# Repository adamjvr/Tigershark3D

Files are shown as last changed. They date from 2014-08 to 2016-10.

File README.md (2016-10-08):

Tigershark3D
============

NOTE: Project has been forked into the Archim project by Ultimachine, its the commercial implementation of the Tigershark 3D printer controller prototype. Learn more here: https://github.com/ultimachine/Archim

A TinyG Powered 3D printer controller for RepRap, based on the RAMBo by Ultimachine, the Arduino DUE, and the TinyG from Synthetos.com

More On TinyG Firmware Here:

AVR Version of TinyG

https://github.com/synthetos/TinyG

ARM Version of TinyG

https://github.com/synthetos/g2

- Powered by the TinyG CNC Firmware from Sythetos.com
- Atmel ATSAM3X8E ARM Cortex M3 (DUE)
- Arduino DUE Compatible
- 5 Texas Instruments DRV8825 Stepper Drivers handle up to 2.5A per phase
- 6 MOSFETs for Heat and fans
- Ti TPIC46L01 Low-Side Automotive MOSFET Driver
- 2 MAX31855EASA+ Thermocouple ADCs
- Two Thermistors
- 2A 3.3V Power for Logic
- 3A 5V power for offboard systems and powering 3.3v Logic regulator
- USB bust power jumperable for firmware flashing purposes
- Firmware flashing via BOSSA
- Max/Min Endstops for 3 Axis
- 6 MOSFETs driven with a gate driver off PWM for heat and fans
- Offboard Expansion Port, generic GPIO expansion, and Kinen interface compatible (https://github.com/kinen/kinen/wiki)
-  True Galvanic Isolation of the USB port and full USB 2.0 Speeds

TinyG 2 ARM Firmware Repository: https://github.com/synthetos/g2

BOSSA Atmel SAM Firmware Flashing Tool: https://github.com/shumatech/BOSSA

Rev2 Update:

Tigershark Rev2 saw a large amount of pin function remapping, mostly to correct the PWM issues int he rev1 board. In addition to the corrections in the circuitry Tigershark has been shrunk and reshaped into the same formfactor and breakout as the RAMBo the board that has heavily inspired Tigershark.

Rev2 2D :
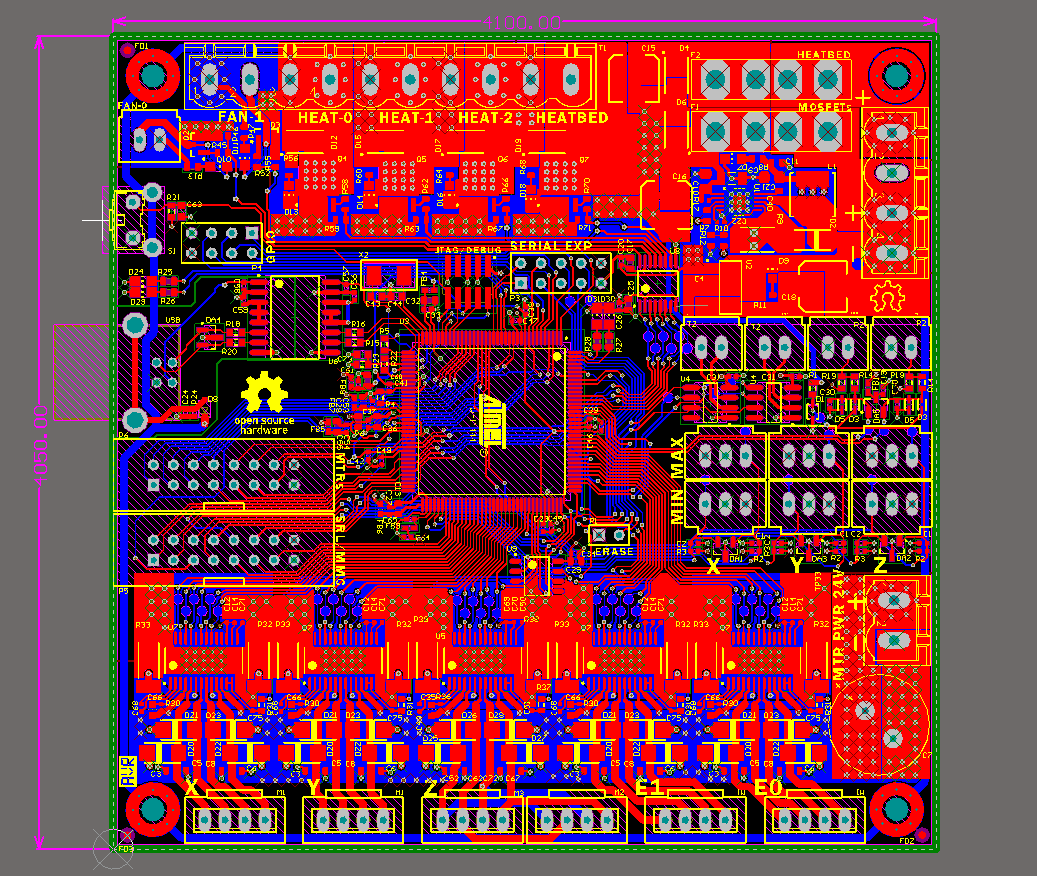
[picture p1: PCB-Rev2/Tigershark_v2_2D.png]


Rev2 3D :
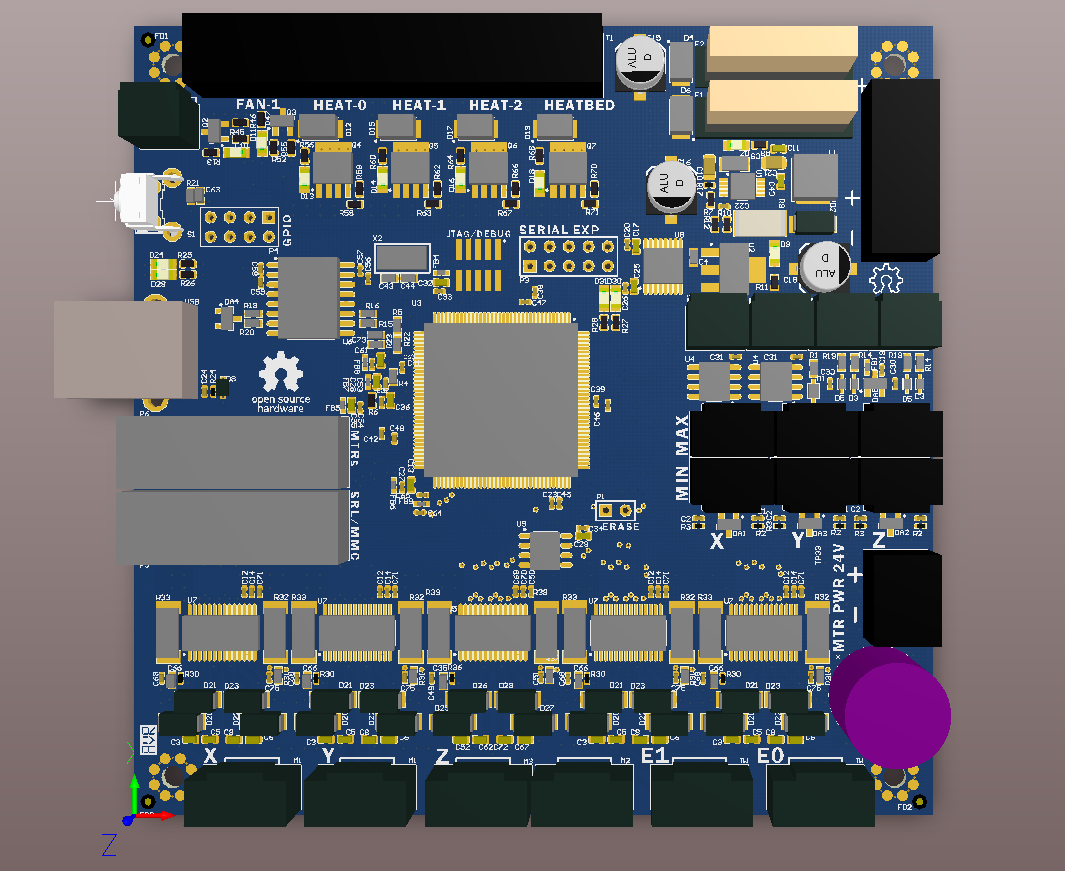
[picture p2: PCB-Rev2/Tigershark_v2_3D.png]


Fabrication Update:

Tigershark rev 1 runs TinyG G2 successfully and connects to Chilipeppr. Rev1 was not without its electrical bugs though, motor ref PWMs for the extruder channels were bound and inverted same issue with two of the mosfets. The rev2 design will have to be repinned to correct these issues. Rev 1 is also too large and expensive and rev2 will see quite a size shrink down and most definitely the same formfactor as the RAMBo. All in all prototype run was successful, all the subsystem circuits have been confirmed and rev2 will be completed soon after. Even though rev2 has to be done to correct the PWM signal issues the plan is to still get rev1 printing so some traces will be cut and jumper wires applied to get it setup to drive a single nozzle reprap.

Rev 1 Fabricated Working Prototype:
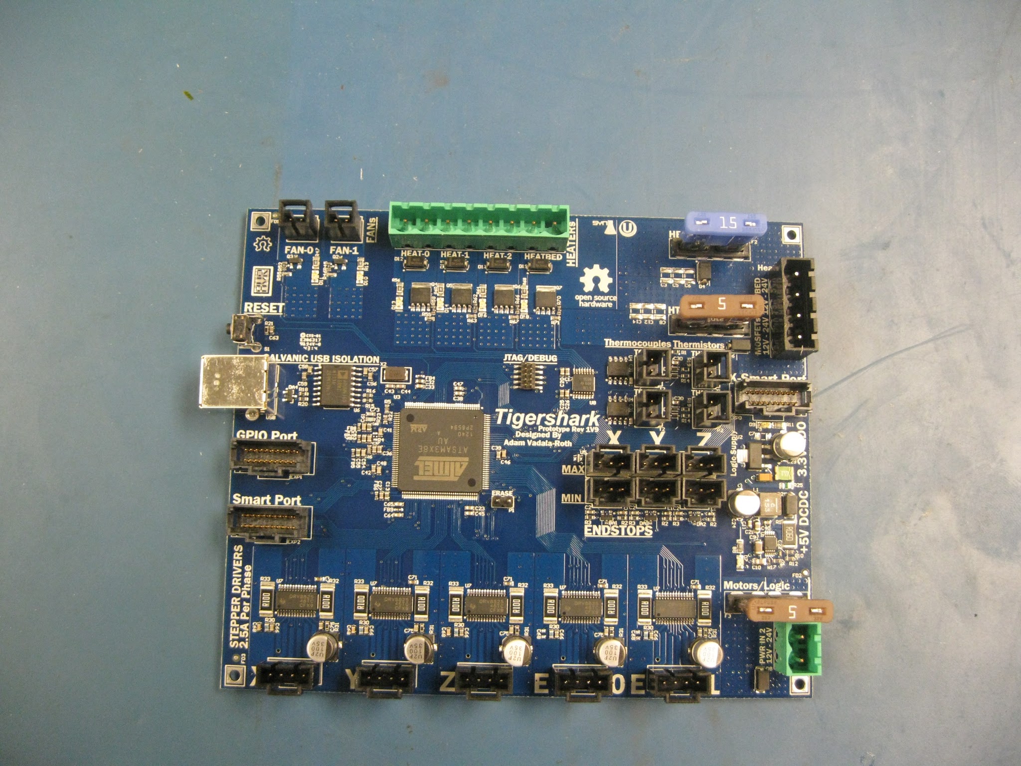
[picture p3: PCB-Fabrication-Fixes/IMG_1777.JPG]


Rev 1 Prototype Design
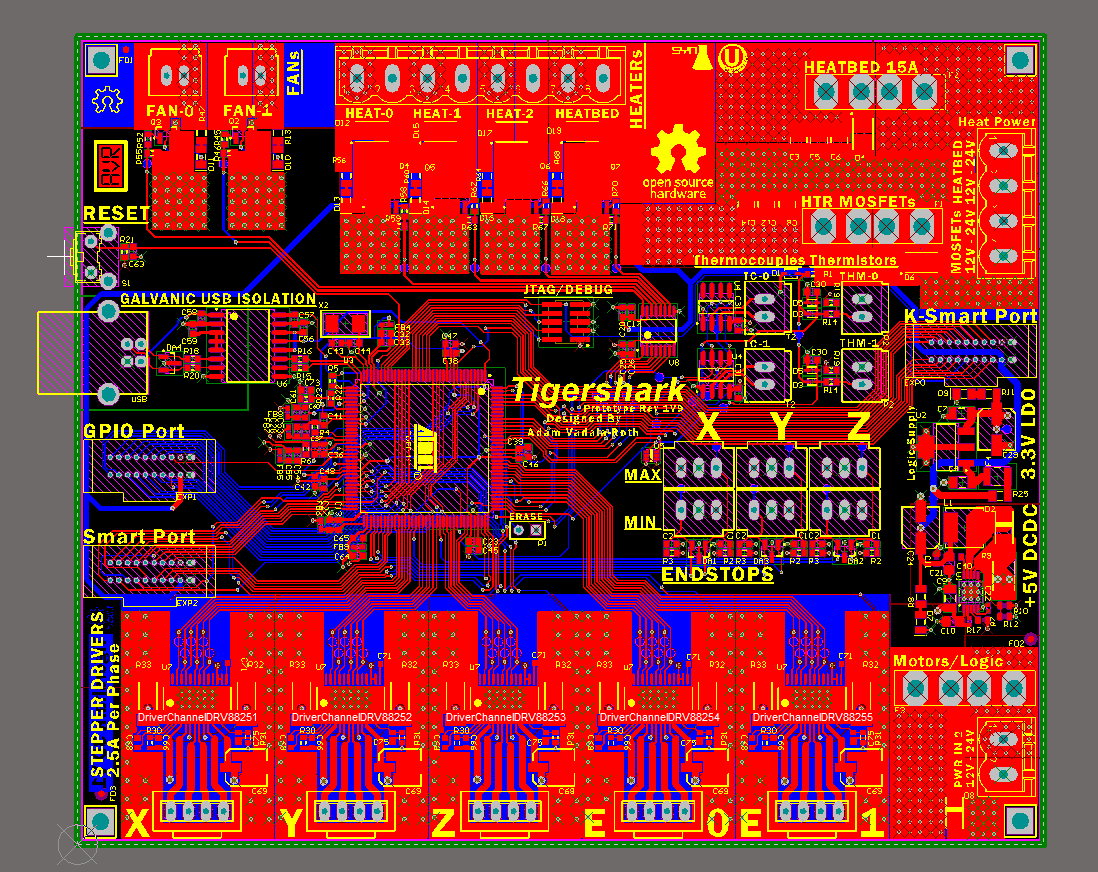
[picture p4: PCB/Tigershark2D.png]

A 3D rendering
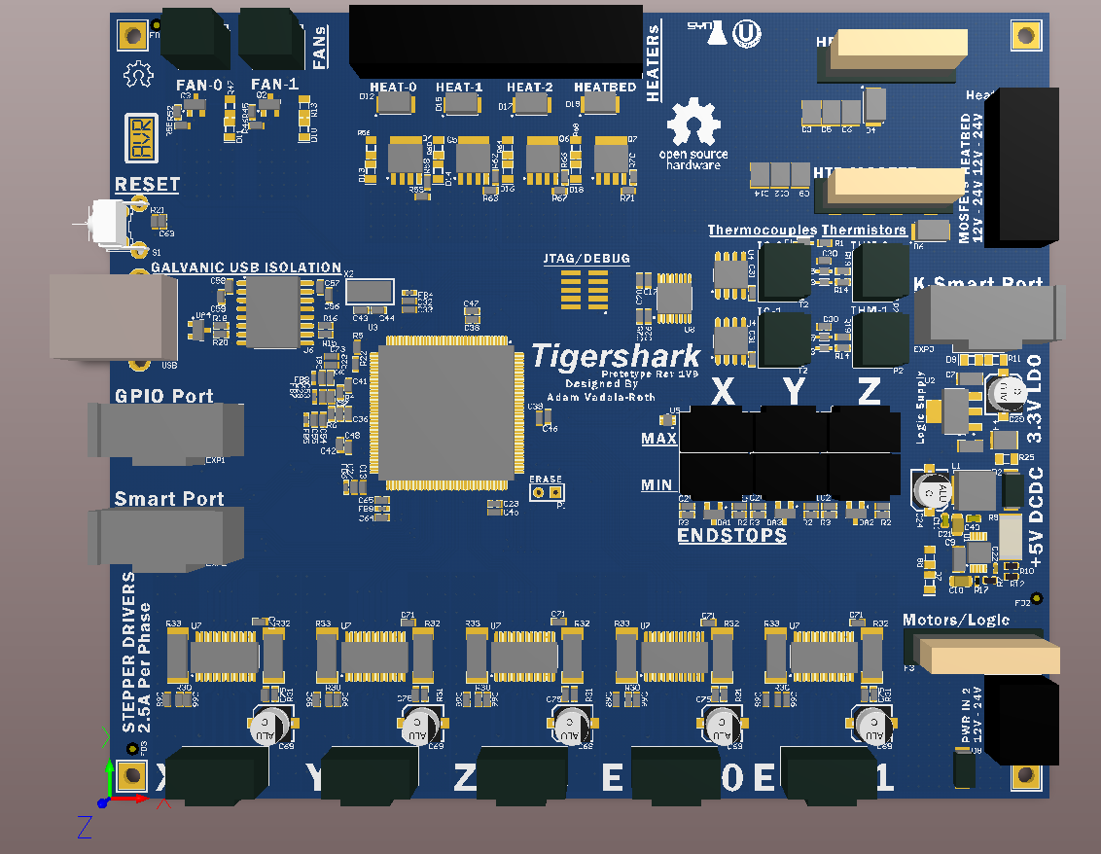
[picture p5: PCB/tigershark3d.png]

Bottom
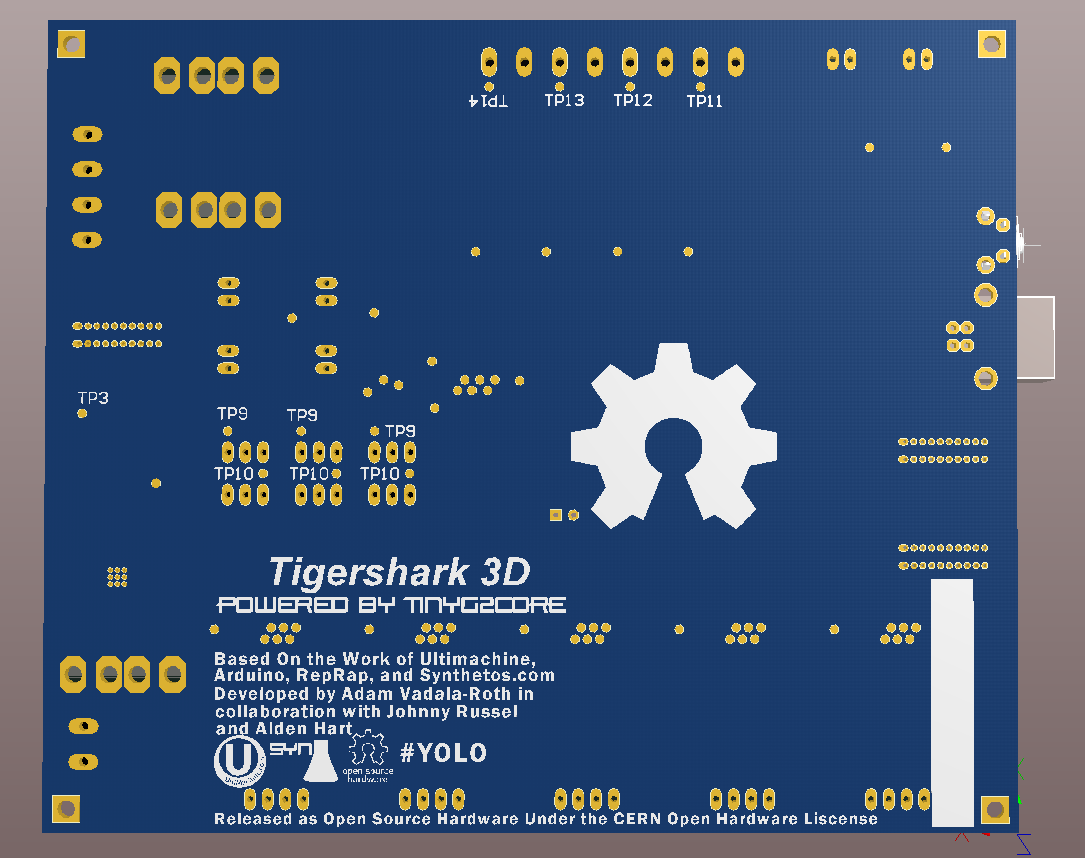
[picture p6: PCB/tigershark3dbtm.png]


Based on the work of:

Arduino

http://arduino.cc/

https://github.com/arduino/Arduino

Ultimachine

https://ultimachine.com

https://github.com/ultimachine/RAMBo

Synthetos

https://sythetos.com

https://github.com/synthetos/g2

https://github.com/synthetos/TinyG

(https://github.com/kinen/kinen/wik

Released as Open Source Hardware Under the CERN Open Hardware Liscense

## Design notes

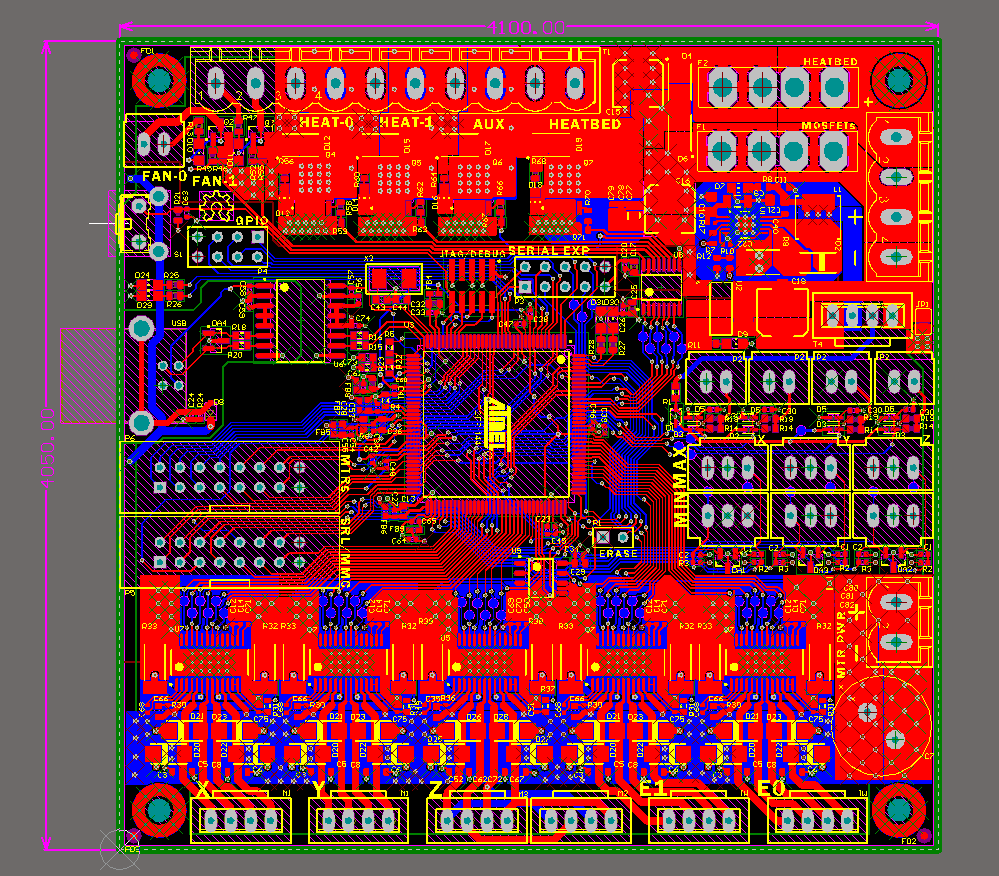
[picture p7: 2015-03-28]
PCB-Rev2/Tigershark_3D_rev2.png

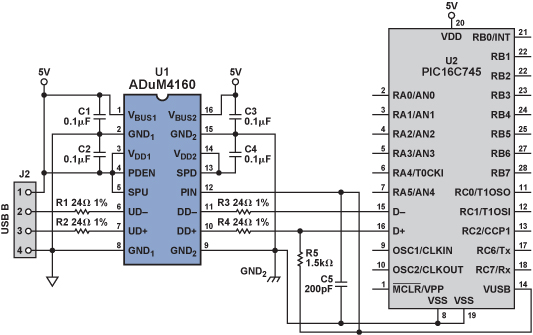
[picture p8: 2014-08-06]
Datasheets/AD43_06_FIG-07.jpg

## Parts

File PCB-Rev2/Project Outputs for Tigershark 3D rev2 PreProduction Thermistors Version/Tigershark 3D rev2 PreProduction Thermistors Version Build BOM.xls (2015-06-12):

Comment | Description | Designator | Digikey # | Footprint | Height | Library Name | LibRef | Manufacturer | MFR | Quantity
4.7nF | CAP CER 0402 4.7nF 25V 10% X7R | C1_ES1 |  | C0402 |  | 3Delight.SCHLIB | CC0402KRX7R8BB472 |  |  | 1
4.7nF | CAP CER 0402 4.7nF 25V 10% X7R | C1_ES2 |  | C0402 |  | 3Delight.SCHLIB | CC0402KRX7R8BB472 |  |  | 1
4.7nF | CAP CER 0402 4.7nF 25V 10% X7R | C1_ES3 |  | C0402 |  | 3Delight.SCHLIB | CC0402KRX7R8BB472 |  |  | 1
4.7nF | CAP CER 0402 4.7nF 25V 10% X7R | C2_ES1 |  | C0402 |  | 3Delight.SCHLIB | CC0402KRX7R8BB472 |  |  | 1
4.7nF | CAP CER 0402 4.7nF 25V 10% X7R | C2_ES2 |  | C0402 |  | 3Delight.SCHLIB | CC0402KRX7R8BB472 |  |  | 1
4.7nF | CAP CER 0402 4.7nF 25V 10% X7R | C2_ES3 |  | C0402 |  | 3Delight.SCHLIB | CC0402KRX7R8BB472 |  |  | 1
10nF | CAP CER 0603 10nF 25V 10% X7R | C3_M1 |  | C0603 |  | 3Delight.SCHLIB | C1608X7R1E103K080AA |  |  | 1
10nF | CAP CER 0603 10nF 25V 10% X7R | C3_M2 |  | C0603 |  | 3Delight.SCHLIB | C1608X7R1E103K080AA |  |  | 1
10nF | CAP CER 0603 10nF 25V 10% X7R | C3_M3 |  | C0603 |  | 3Delight.SCHLIB | C1608X7R1E103K080AA |  |  | 1
10nF | CAP CER 0603 10nF 25V 10% X7R | C3_M4 |  | C0603 |  | 3Delight.SCHLIB | C1608X7R1E103K080AA |  |  | 1
47uF | CAP CER 47UF 6.3V 20% X5R 0805 | C4 |  | C0805 |  | Tigershark3D.SchLib | CL21A476MQCLRNC | Samsung |  | 1
10nF | CAP CER 0603 10nF 25V 10% X7R | C5_M1 |  | C0603 |  | 3Delight.SCHLIB | C1608X7R1E103K080AA |  |  | 1
10nF | CAP CER 0603 10nF 25V 10% X7R | C5_M2 |  | C0603 |  | 3Delight.SCHLIB | C1608X7R1E103K080AA |  |  | 1
10nF | CAP CER 0603 10nF 25V 10% X7R | C5_M3 |  | C0603 |  | 3Delight.SCHLIB | C1608X7R1E103K080AA |  |  | 1
10nF | CAP CER 0603 10nF 25V 10% X7R | C5_M4 |  | C0603 |  | 3Delight.SCHLIB | C1608X7R1E103K080AA |  |  | 1
10nF | CAP CER 0603 10nF 25V 10% X7R | C6_M1 |  | C0603 |  | 3Delight.SCHLIB | C1608X7R1E103K080AA |  |  | 1
10nF | CAP CER 0603 10nF 25V 10% X7R | C6_M2 |  | C0603 |  | 3Delight.SCHLIB | C1608X7R1E103K080AA |  |  | 1
10nF | CAP CER 0603 10nF 25V 10% X7R | C6_M3 |  | C0603 |  | 3Delight.SCHLIB | C1608X7R1E103K080AA |  |  | 1
10nF | CAP CER 0603 10nF 25V 10% X7R | C6_M4 |  | C0603 |  | 3Delight.SCHLIB | C1608X7R1E103K080AA |  |  | 1
470uF | CAP ALU 470uF 50V 20% | C7 |  | C12,5-5 |  | Tigershark3D.SchLib | UPW1H471MHD1TO |  |  | 1
10nF | CAP CER 0603 10nF 25V 10% X7R | C8_M1 |  | C0603 |  | 3Delight.SCHLIB | C1608X7R1E103K080AA |  |  | 1
10nF | CAP CER 0603 10nF 25V 10% X7R | C8_M2 |  | C0603 |  | 3Delight.SCHLIB | C1608X7R1E103K080AA |  |  | 1
10nF | CAP CER 0603 10nF 25V 10% X7R | C8_M3 |  | C0603 |  | 3Delight.SCHLIB | C1608X7R1E103K080AA |  |  | 1
10nF | CAP CER 0603 10nF 25V 10% X7R | C8_M4 |  | C0603 |  | 3Delight.SCHLIB | C1608X7R1E103K080AA |  |  | 1
4.7uF | CAP CER 1206 4.7uF 50V 10% X5R | C9 |  | C1206 |  | 3Delight.SCHLIB | C1206C475K5PACTU |  |  | 1
1uF | CAP CER 0805 1uF 50V 10% X7R | C10 |  | C0805 |  | 3Delight.SCHLIB | GRM21BR71H105KA12L |  |  | 1
100nF | CAP CER 0603 100nF 50V 10% X7R | C11 |  | C0603 |  | 3Delight.SCHLIB | C0603C104K5RACTU |  |  | 1
0402 | Capacitor (Semiconductor SIM Model) | C12_M1 |  | C0402 | 0.5 ±0.05mm | Tigershark3D.SchLib | 100nF C0402 - GRM155R71C104KA88D |  | Murata | 1
0402 | Capacitor (Semiconductor SIM Model) | C12_M2 |  | C0402 | 0.5 ±0.05mm | Tigershark3D.SchLib | 100nF C0402 - GRM155R71C104KA88D |  | Murata | 1
0402 | Capacitor (Semiconductor SIM Model) | C12_M3 |  | C0402 | 0.5 ±0.05mm | Tigershark3D.SchLib | 100nF C0402 - GRM155R71C104KA88D |  | Murata | 1
0402 | Capacitor (Semiconductor SIM Model) | C12_M4 |  | C0402 | 0.5 ±0.05mm | Tigershark3D.SchLib | 100nF C0402 - GRM155R71C104KA88D |  | Murata | 1
0603 | CAP CER 10UF 6.3V 10% JB 0603 | C13 | 445-11185-1-ND | C0603 | 0.9mm | Tigershark3D.SchLib | C1608JB0J106K080AB |  | TDK | 1
0402 | Capacitor (Semiconductor SIM Model) | C14_M1 |  | C0402 | 0.5 ±0.05mm | Tigershark3D.SchLib | 100nF C0402 - GRM155R71C104KA88D |  | Murata | 1
0402 | Capacitor (Semiconductor SIM Model) | C14_M2 |  | C0402 | 0.5 ±0.05mm | Tigershark3D.SchLib | 100nF C0402 - GRM155R71C104KA88D |  | Murata | 1
0402 | Capacitor (Semiconductor SIM Model) | C14_M3 |  | C0402 | 0.5 ±0.05mm | Tigershark3D.SchLib | 100nF C0402 - GRM155R71C104KA88D |  | Murata | 1
0402 | Capacitor (Semiconductor SIM Model) | C14_M4 |  | C0402 | 0.5 ±0.05mm | Tigershark3D.SchLib | 100nF C0402 - GRM155R71C104KA88D |  | Murata | 1
EEE-1VA101XP | CAP ALUM 100UF 35V 20% SMD | C15 |  | EEE-1VA101XP | 7.70mm | Tigershark3D.SchLib | EEE-1VA101XP |  |  | 1
EEE-1VA101XP | CAP ALUM 100UF 35V 20% SMD | C16 |  | EEE-1VA101XP | 7.70mm | Tigershark3D.SchLib | EEE-1VA101XP |  |  | 1
0603 | CAP CER 10UF 6.3V 10% JB 0603 | C17 | 445-11185-1-ND | C0603 | 0.9mm | Tigershark3D.SchLib | C1608JB0J106K080AB |  | TDK | 1
EEE-1VA101XP | CAP ALUM 100UF 35V 20% SMD | C18 |  | EEE-1VA101XP | 7.70mm | Tigershark3D.SchLib | EEE-1VA101XP |  |  | 1
4.7nF | CAP CER 0402 4.7nF 25V 10% X7R | C19 |  | C0402 |  | 3Delight.SCHLIB | CC0402KRX7R8BB472 |  |  | 1
0402 | CAP CER 0.1UF (100nF) 16V 10% X7R 0402 | C20 |  | C0402 | 0.5 ±0.05mm | Tigershark3D.SchLib | GRM155R71C104KA88D |  | Murata | 1
10uF | CAP CER 0805 10uF 10V 10% X5R | C21 |  | C0805 |  | 3Delight.SCHLIB | C0805C106K8PACTU |  |  | 1
1uF | CAP CER 0402 1uF 6.3V 10% X5R | C22 |  | C0402 |  | 3Delight.SCHLIB | GRM155R60J105KE19D |  |  | 1
100nF | CAP CER 0402 100nF 16V 10% X7R | C23 |  | C0402 |  | 3Delight.SCHLIB | GRM155R71C104KA88D |  |  | 1
0402 | 0.47uF 6.3v C0402 - GRM155R60J474KE19D | C24 |  | C0402 | 0.5 ±0.05mm | Tigershark3D.SchLib | GRM155R60J474KE19D |  | Murata | 1
0603 | CAP CER 10UF 6.3V 10% JB 0603 | C25 | 445-11185-1-ND | C0603 | 0.9mm | Tigershark3D.SchLib | C1608JB0J106K080AB |  | TDK | 1
0402 | CAP CER 0.1UF (100nF) 16V 10% X7R 0402 | C26 |  | C0402 | 0.5 ±0.05mm | Tigershark3D.SchLib | GRM155R71C104KA88D |  | Murata | 1
100nF | CAP CER 0402 100nF 16V 10% X7R | C27 |  | C0402 |  | 3Delight.SCHLIB | GRM155R71C104KA88D |  |  | 1
0603 | CAP CER 10UF 6.3V 10% JB 0603 | C28 | 445-11185-1-ND | C0603 | 0.9mm | Tigershark3D.SchLib | C1608JB0J106K080AB |  | TDK | 1
100nF | CAP CER 0402 100nF 16V 10% X7R | C30_TR1 |  | C0402 |  | 3Delight.SCHLIB | GRM155R71C104KA88D |  |  | 1
100nF | CAP CER 0402 100nF 16V 10% X7R | C30_TR2 |  | C0402 |  | 3Delight.SCHLIB | GRM155R71C104KA88D |  |  | 1
100nF | CAP CER 0402 100nF 16V 10% X7R | C30_TR3 |  | C0402 |  | 3Delight.SCHLIB | GRM155R71C104KA88D |  |  | 1
100nF | CAP CER 0402 100nF 16V 10% X7R | C30_TR4 |  | C0402 |  | 3Delight.SCHLIB | GRM155R71C104KA88D |  |  | 1
0603 | CAP CER 10UF 6.3V 10% JB 0603 | C32 | 445-11185-1-ND | C0603 | 0.9mm | Tigershark3D.SchLib | C1608JB0J106K080AB |  | TDK | 1
100nF | CAP CER 0402 100nF 16V 10% X7R | C33 |  | C0402 |  | 3Delight.SCHLIB | GRM155R71C104KA88D |  |  | 1
100nF | CAP CER 0402 100nF 16V 10% X7R | C34 |  | C0402 |  | 3Delight.SCHLIB | GRM155R71C104KA88D |  |  | 1
100nF | CAP CER 0603 100nF 50V 10% X7R | C35 |  | C0603 |  | 3Delight.SCHLIB | C0603C104K5RACTU |  |  | 1
0603 | CAP CER 10UF 6.3V 10% JB 0603 | C36 | 445-11185-1-ND | C0603 | 0.9mm | Tigershark3D.SchLib | C1608JB0J106K080AB |  | TDK | 1
100nF | CAP CER 0402 100nF 16V 10% X7R | C37 |  | C0402 |  | 3Delight.SCHLIB | GRM155R71C104KA88D |  |  | 1
100nF | CAP CER 0402 100nF 16V 10% X7R | C38 |  | C0402 |  | 3Delight.SCHLIB | GRM155R71C104KA88D |  |  | 1
100nF | CAP CER 0402 100nF 16V 10% X7R | C39 |  | C0402 |  | 3Delight.SCHLIB | GRM155R71C104KA88D |  |  | 1
100nF | CAP CER 0603 100nF 50V 10% X7R | C40 |  | C0603 |  | 3Delight.SCHLIB | C0603C104K5RACTU |  |  | 1
100nF | CAP CER 0402 100nF 16V 10% X7R | C41 |  | C0402 |  | 3Delight.SCHLIB | GRM155R71C104KA88D |  |  | 1
100nF | CAP CER 0402 100nF 16V 10% X7R | C42 |  | C0402 |  | 3Delight.SCHLIB | GRM155R71C104KA88D |  |  | 1
0402 | CAP CER 10PF 50V 5% NP0 0402 | C43 |  | C0402 | 0.55mm | Tigershark3D.SchLib | CL05C100JB5NNNC |  | Samsung | 1
0402 | CAP CER 10PF 50V 5% NP0 0402 | C44 |  | C0402 | 0.55mm | Tigershark3D.SchLib | CL05C100JB5NNNC |  | Samsung | 1
100nF | CAP CER 0402 100nF 16V 10% X7R | C45 |  | C0402 |  | 3Delight.SCHLIB | GRM155R71C104KA88D |  |  | 1
100nF | CAP CER 0402 100nF 16V 10% X7R | C46 |  | C0402 |  | 3Delight.SCHLIB | GRM155R71C104KA88D |  |  | 1
100nF | CAP CER 0402 100nF 16V 10% X7R | C47 |  | C0402 |  | 3Delight.SCHLIB | GRM155R71C104KA88D |  |  | 1
100nF | CAP CER 0402 100nF 16V 10% X7R | C48 |  | C0402 |  | 3Delight.SCHLIB | GRM155R71C104KA88D |  |  | 1
0402 | CAP CER 10000PF 50V X7R 0402 | C49 | 490-7763-1-ND | C0402 | 0.5 ±0.05mm | Tigershark3D.SchLib | GRM155R71H103JA88D |  | Murata | 1
0402 | 0.47uF 6.3v C0402 - GRM155R60J474KE19D | C50 |  | C0402 | 0.5 ±0.05mm | Tigershark3D.SchLib | GRM155R60J474KE19D |  | Murata | 1
0402 | Capacitor (Semiconductor SIM Model) | C51 |  | C0402 | 0.5 ±0.05mm | Tigershark3D.SchLib | 100nF C0402 - GRM155R71C104KA88D |  | Murata | 1
10nF | CAP CER 0603 10nF 25V 10% X7R | C52 |  | C0603 |  | 3Delight.SCHLIB | C1608X7R1E103K080AA |  |  | 1
100nF | CAP CER 0402 100nF 16V 10% X7R | C53 |  | C0402 |  | 3Delight.SCHLIB | GRM155R71C104KA88D |  |  | 1
100nF | CAP CER 0402 100nF 16V 10% X7R | C54 |  | C0402 |  | 3Delight.SCHLIB | GRM155R71C104KA88D |  |  | 1
0603 | CAP CER 10UF 6.3V 10% JB 0603 | C55 | 445-11185-1-ND | C0603 | 0.9mm | Tigershark3D.SchLib | C1608JB0J106K080AB |  | TDK | 1
100nF | CAP CER 0402 100nF 16V 10% X7R | C56 |  | C0402 |  | 3Delight.SCHLIB | GRM155R71C104KA88D |  |  | 1
100nF | CAP CER 0402 100nF 16V 10% X7R | C57 |  | C0402 |  | 3Delight.SCHLIB | GRM155R71C104KA88D |  |  | 1
100nF | CAP CER 0402 100nF 16V 10% X7R | C58 |  | C0402 |  | 3Delight.SCHLIB | GRM155R71C104KA88D |  |  | 1
100nF | CAP CER 0402 100nF 16V 10% X7R | C59 |  | C0402 |  | 3Delight.SCHLIB | GRM155R71C104KA88D |  |  | 1
0603 | CAP CER 10UF 6.3V 10% JB 0603 | C60 | 445-11185-1-ND | C0603 | 0.9mm | Tigershark3D.SchLib | C1608JB0J106K080AB |  | TDK | 1
100nF | CAP CER 0402 100nF 16V 10% X7R | C61 |  | C0402 |  | 3Delight.SCHLIB | GRM155R71C104KA88D |  |  | 1
10nF | CAP CER 0603 10nF 25V 10% X7R | C62 |  | C0603 |  | 3Delight.SCHLIB | C1608X7R1E103K080AA |  |  | 1
0402 | Capacitor (Semiconductor SIM Model) | C63 |  | C0402 | 0.5 ±0.05mm | Tigershark3D.SchLib | 100nF C0402 - GRM155R71C104KA88D |  | Murata | 1
100nF | CAP CER 0402 100nF 16V 10% X7R | C64 |  | C0402 |  | 3Delight.SCHLIB | GRM155R71C104KA88D |  |  | 1
100nF | CAP CER 0402 100nF 16V 10% X7R | C65 |  | C0402 |  | 3Delight.SCHLIB | GRM155R71C104KA88D |  |  | 1
100nF | CAP CER 0603 100nF 50V 10% X7R | C66_M1 |  | C0603 |  | 3Delight.SCHLIB | C0603C104K5RACTU |  |  | 1
100nF | CAP CER 0603 100nF 50V 10% X7R | C66_M2 |  | C0603 |  | 3Delight.SCHLIB | C0603C104K5RACTU |  |  | 1
100nF | CAP CER 0603 100nF 50V 10% X7R | C66_M3 |  | C0603 |  | 3Delight.SCHLIB | C0603C104K5RACTU |  |  | 1
100nF | CAP CER 0603 100nF 50V 10% X7R | C66_M4 |  | C0603 |  | 3Delight.SCHLIB | C0603C104K5RACTU |  |  | 1
10nF | CAP CER 0603 10nF 25V 10% X7R | C67 |  | C0603 |  | 3Delight.SCHLIB | C1608X7R1E103K080AA |  |  | 1
0402 | CAP CER 10000PF 50V X7R 0402 | C68_M1 | 490-7763-1-ND | C0402 | 0.5 ±0.05mm | Tigershark3D.SchLib | GRM155R71H103JA88D |  | Murata | 1
0402 | CAP CER 10000PF 50V X7R 0402 | C68_M2 | 490-7763-1-ND | C0402 | 0.5 ±0.05mm | Tigershark3D.SchLib | GRM155R71H103JA88D |  | Murata | 1
0402 | CAP CER 10000PF 50V X7R 0402 | C68_M3 | 490-7763-1-ND | C0402 | 0.5 ±0.05mm | Tigershark3D.SchLib | GRM155R71H103JA88D |  | Murata | 1
0402 | CAP CER 10000PF 50V X7R 0402 | C68_M4 | 490-7763-1-ND | C0402 | 0.5 ±0.05mm | Tigershark3D.SchLib | GRM155R71H103JA88D |  | Murata | 1
0402 | Capacitor (Semiconductor SIM Model) | C69 |  | C0402 | 0.5 ±0.05mm | Tigershark3D.SchLib | 100nF C0402 - GRM155R71C104KA88D |  | Murata | 1
0402 | Capacitor (Semiconductor SIM Model) | C70 |  | C0402 | 0.5 ±0.05mm | Tigershark3D.SchLib | 100nF C0402 - GRM155R71C104KA88D |  | Murata | 1
0402 | 0.47uF 6.3v C0402 - GRM155R60J474KE19D | C71_M1 |  | C0402 | 0.5 ±0.05mm | Tigershark3D.SchLib | GRM155R60J474KE19D |  | Murata | 1
0402 | 0.47uF 6.3v C0402 - GRM155R60J474KE19D | C71_M2 |  | C0402 | 0.5 ±0.05mm | Tigershark3D.SchLib | GRM155R60J474KE19D |  | Murata | 1
0402 | 0.47uF 6.3v C0402 - GRM155R60J474KE19D | C71_M3 |  | C0402 | 0.5 ±0.05mm | Tigershark3D.SchLib | GRM155R60J474KE19D |  | Murata | 1
0402 | 0.47uF 6.3v C0402 - GRM155R60J474KE19D | C71_M4 |  | C0402 | 0.5 ±0.05mm | Tigershark3D.SchLib | GRM155R60J474KE19D |  | Murata | 1
10nF | CAP CER 0603 10nF 25V 10% X7R | C72 |  | C0603 |  | 3Delight.SCHLIB | C1608X7R1E103K080AA |  |  | 1
0402 | CAP CER 22PF 50V 5% NP0 0402 | C73 |  | C0402 | 0.55mm | Tigershark3D.SchLib | CL05C220JB5NNNC |  | Samsung | 1
100nF | CAP CER 0402 100nF 16V 10% X7R | C74 |  | C0402 |  | 3Delight.SCHLIB | GRM155R71C104KA88D |  |  | 1
0402 | Capacitor (Semiconductor SIM Model) | C75_M1 |  | C0402 | 0.5 ±0.05mm | Tigershark3D.SchLib | 100nF C0402 - GRM155R71C104KA88D |  | Murata | 1
0402 | Capacitor (Semiconductor SIM Model) | C75_M2 |  | C0402 | 0.5 ±0.05mm | Tigershark3D.SchLib | 100nF C0402 - GRM155R71C104KA88D |  | Murata | 1
0402 | Capacitor (Semiconductor SIM Model) | C75_M3 |  | C0402 | 0.5 ±0.05mm | Tigershark3D.SchLib | 100nF C0402 - GRM155R71C104KA88D |  | Murata | 1
0402 | Capacitor (Semiconductor SIM Model) | C75_M4 |  | C0402 | 0.5 ±0.05mm | Tigershark3D.SchLib | 100nF C0402 - GRM155R71C104KA88D |  | Murata | 1
10uF 50V | CAP CER 10UF 50V 10% X5R 1206 | C77 |  | C1206 |  | Tigershark3D.SchLib | CL31A106KBHNNNE | Samsung |  | 1
0.1uF 50V | CAP CER 0.1UF 50V 10% X7R 0603 | C78 |  | C0603 |  | Tigershark3D.SchLib | CL10B104KB8SFNC |  |  | 1
0402 | CAP CER 10000PF 50V 5% X7R 0402 | C79 |  | C0402 | 0.25 ± 0.15mm | Tigershark3D.SchLib | CL05B103JB5NNNC | Samsung |  | 1
10uF 50V | CAP CER 10UF 50V 10% X5R 1206 | C80 |  | C1206 |  | Tigershark3D.SchLib | CL31A106KBHNNNE | Samsung |  | 1
0.1uF 50V | CAP CER 0.1UF 50V 10% X7R 0603 | C81 |  | C0603 |  | Tigershark3D.SchLib | CL10B104KB8SFNC |  |  | 1
0402 | CAP CER 10000PF 50V 5% X7R 0402 | C82 |  | C0402 | 0.25 ± 0.15mm | Tigershark3D.SchLib | CL05B103JB5NNNC | Samsung |  | 1
0603 | CAP CER 10UF 6.3V 10% JB 0603 | C? | 445-11185-1-ND | C0603 | 0.9mm | Tigershark3D.SchLib | C1608JB0J106K080AB |  | TDK | 1
SZMM3Z4V7T1G | Zener Diode | D1 |  | SZMM3Z4V7T1G |  | Miscellaneous Devices.IntLib | D Zener |  |  | 1
SK310A-TP | DIODE Schottky 3A SMA | D2 |  | SMA-SM |  | 3Delight.SCHLIB | SK310A |  |  | 1
1N4148WT | DIODE SOD523 | D3_TR1 |  | SOD523 |  | 3Delight.SCHLIB | 1N4148WT |  |  | 1
1N4148WT | DIODE SOD523 | D3_TR2 |  | SOD523 |  | 3Delight.SCHLIB | 1N4148WT |  |  | 1
1N4148WT | DIODE SOD523 | D3_TR3 |  | SOD523 |  | 3Delight.SCHLIB | 1N4148WT |  |  | 1
1N4148WT | DIODE SOD523 | D3_TR4 |  | SOD523 |  | 3Delight.SCHLIB | 1N4148WT |  |  | 1
S3A-13-F | DIODE DO-214AB | D4 |  | DO-214AB |  | 3Delight.SCHLIB | S3A-13-F |  |  | 1
1N4148WT | DIODE SOD523 | D5_TR1 |  | SOD523 |  | 3Delight.SCHLIB | 1N4148WT |  |  | 1
1N4148WT | DIODE SOD523 | D5_TR2 |  | SOD523 |  | 3Delight.SCHLIB | 1N4148WT |  |  | 1
1N4148WT | DIODE SOD523 | D5_TR3 |  | SOD523 |  | 3Delight.SCHLIB | 1N4148WT |  |  | 1
1N4148WT | DIODE SOD523 | D5_TR4 |  | SOD523 |  | 3Delight.SCHLIB | 1N4148WT |  |  | 1
S3A-13-F | DIODE DO-214AB | D6 |  | DO-214AB |  | 3Delight.SCHLIB | S3A-13-F |  |  | 1
S3A-13-F | DIODE DO-214AB | D7 |  | DO-214AB |  | 3Delight.SCHLIB | S3A-13-F |  |  | 1
RSB39VTE-17 | DIODE TVS | D8 |  | SOD323-R |  | Tigershark3D.SchLib | RSB39VTE-17 |  |  | 1
RSB39VTE-17 | DIODE TVS | D9 |  | SOD323-R |  | 3Delight.SCHLIB | RSB39VTE-17 |  |  | 1
5988140107F | LED 0805 Yellow | D10 |  | LED2012120 |  | Tigershark3D.SchLib | 5988140107F |  |  | 1
5988140107F | LED 0805 Yellow | D11 |  | LED2012120 |  | Tigershark3D.SchLib | 5988140107F |  |  | 1
B240A-13-F | Schottky Diode | D12 |  | SK310A-TP |  | Miscellaneous Devices.IntLib | D Schottky |  |  | 1
5988140107F | LED 0805 Yellow | D13 |  | LED2012120 |  | Tigershark3D.SchLib | 5988140107F |  |  | 1
5988140107F | LED 0805 Yellow | D14 |  | LED2012120 |  | Tigershark3D.SchLib | 5988140107F |  |  | 1
B240A-13-F | Schottky Diode | D15 |  | SK310A-TP |  | Miscellaneous Devices.IntLib | D Schottky |  |  | 1
5988140107F | LED 0805 Yellow | D16 |  | LED2012120 |  | Tigershark3D.SchLib | 5988140107F |  |  | 1
B240A-13-F | Schottky Diode | D17 |  | SK310A-TP |  | Miscellaneous Devices.IntLib | D Schottky |  |  | 1
5988140107F | LED 0805 Yellow | D18 |  | LED2012120 |  | Tigershark3D.SchLib | 5988140107F |  |  | 1
B240A-13-F | Schottky Diode | D19 |  | SK310A-TP |  | Miscellaneous Devices.IntLib | D Schottky |  |  | 1
SMAJ30A | DIODE TVS 30V SMA | D20_M1 |  | SMA-SM |  | Tigershark3D.SchLib | SMAJ30A |  |  | 1
SMAJ30A | DIODE TVS 30V SMA | D20_M2 |  | SMA-SM |  | Tigershark3D.SchLib | SMAJ30A |  |  | 1
SMAJ30A | DIODE TVS 30V SMA | D20_M3 |  | SMA-SM |  | Tigershark3D.SchLib | SMAJ30A |  |  | 1
SMAJ30A | DIODE TVS 30V SMA | D20_M4 |  | SMA-SM |  | Tigershark3D.SchLib | SMAJ30A |  |  | 1
SMAJ30A | DIODE TVS 30V SMA | D21_M1 |  | SMA-SM |  | Tigershark3D.SchLib | SMAJ30A |  |  | 1
SMAJ30A | DIODE TVS 30V SMA | D21_M2 |  | SMA-SM |  | Tigershark3D.SchLib | SMAJ30A |  |  | 1
SMAJ30A | DIODE TVS 30V SMA | D21_M3 |  | SMA-SM |  | Tigershark3D.SchLib | SMAJ30A |  |  | 1
SMAJ30A | DIODE TVS 30V SMA | D21_M4 |  | SMA-SM |  | Tigershark3D.SchLib | SMAJ30A |  |  | 1
SMAJ30A | DIODE TVS 30V SMA | D22_M1 |  | SMA-SM |  | Tigershark3D.SchLib | SMAJ30A |  |  | 1
SMAJ30A | DIODE TVS 30V SMA | D22_M2 |  | SMA-SM |  | Tigershark3D.SchLib | SMAJ30A |  |  | 1
SMAJ30A | DIODE TVS 30V SMA | D22_M3 |  | SMA-SM |  | Tigershark3D.SchLib | SMAJ30A |  |  | 1
SMAJ30A | DIODE TVS 30V SMA | D22_M4 |  | SMA-SM |  | Tigershark3D.SchLib | SMAJ30A |  |  | 1
SMAJ30A | DIODE TVS 30V SMA | D23_M1 |  | SMA-SM |  | Tigershark3D.SchLib | SMAJ30A |  |  | 1
SMAJ30A | DIODE TVS 30V SMA | D23_M2 |  | SMA-SM |  | Tigershark3D.SchLib | SMAJ30A |  |  | 1
SMAJ30A | DIODE TVS 30V SMA | D23_M3 |  | SMA-SM |  | Tigershark3D.SchLib | SMAJ30A |  |  | 1
SMAJ30A | DIODE TVS 30V SMA | D23_M4 |  | SMA-SM |  | Tigershark3D.SchLib | SMAJ30A |  |  | 1
5988140107F | LED 0805 Yellow | D24 |  | LED2012120 |  | Tigershark3D.SchLib | 5988140107F |  |  | 1
SMAJ30A | DIODE TVS 30V SMA | D25 |  | SMA-SM |  | Tigershark3D.SchLib | SMAJ30A |  |  | 1
SMAJ30A | DIODE TVS 30V SMA | D26 |  | SMA-SM |  | Tigershark3D.SchLib | SMAJ30A |  |  | 1
SMAJ30A | DIODE TVS 30V SMA | D27 |  | SMA-SM |  | Tigershark3D.SchLib | SMAJ30A |  |  | 1
SMAJ30A | DIODE TVS 30V SMA | D28 |  | SMA-SM |  | Tigershark3D.SchLib | SMAJ30A |  |  | 1
5988140107F | LED 0805 Yellow | D29 |  | LED2012120 |  | Tigershark3D.SchLib | 5988140107F |  |  | 1
PESDxL2BT | PESDxL2BT TVS Diode Array 2x | DA1 |  | SOT95P230X110-3N |  | ZMBo Schematic Library.SchLib | PESDxL2BT |  |  | 1
PESDxL2BT | PESDxL2BT TVS Diode Array 2x | DA2 |  | SOT95P230X110-3N |  | ZMBo Schematic Library.SchLib | PESDxL2BT |  |  | 1
PESDxL2BT | PESDxL2BT TVS Diode Array 2x | DA3 |  | SOT95P230X110-3N |  | ZMBo Schematic Library.SchLib | PESDxL2BT |  |  | 1
PESDxL2BT | PESDxL2BT TVS Diode Array 2x | DA4 |  | SOT95P230X110-3N |  | ZMBo Schematic Library.SchLib | PESDxL2BT |  |  | 1
3557-2 | FUSE PTH ATO | F1 |  | 3557 |  | 3Delight.SCHLIB | 3557-2 |  |  | 1
3557-2 | FUSE PTH ATO | F2 |  | 3557 |  | 3Delight.SCHLIB | 3557-2 |  |  | 1
3557-2 | FUSE PTH ATO | F3 |  | 3557 |  | 3Delight.SCHLIB | 3557-2 |  |  | 1
Molex 70543-02 | Molex 70543-02 | FAN-1 |  | 70543-02 |  | ZMBo Schematic Library.SchLib | Molex 70543-02 |  |  | 1
BLM15HG601SN1D | BLM15HG601SN1D | FB4 |  | BLM18PG121SN1D |  | AHD Part Library.SchLib | BLM15HG601SN1D |  |  | 1
BLM15HG601SN1D | BLM15HG601SN1D | FB5 |  | BLM18PG121SN1D |  | AHD Part Library.SchLib | BLM15HG601SN1D |  |  | 1
BLM15HG601SN1D | BLM15HG601SN1D | FB6 |  | BLM18PG121SN1D |  | AHD Part Library.SchLib | BLM15HG601SN1D |  |  | 1
BLM15HG601SN1D | BLM15HG601SN1D | FB7 |  | BLM18PG121SN1D |  | AHD Part Library.SchLib | BLM15HG601SN1D |  |  | 1
BLM15HG601SN1D | BLM15HG601SN1D | FB8 |  | BLM18PG121SN1D |  | AHD Part Library.SchLib | BLM15HG601SN1D |  |  | 1
BLM15HG601SN1D | BLM15HG601SN1D | FB9 |  | BLM18PG121SN1D |  | AHD Part Library.SchLib | BLM15HG601SN1D |  |  | 1
FIDUCIAL |  | FD1 |  | FIDUCIAL-1X2 |  | ZMBo Schematic Library.SchLib | FIDUCIAL |  |  | 1
FIDUCIAL |  | FD2 |  | FIDUCIAL-1X2 |  | ZMBo Schematic Library.SchLib | FIDUCIAL |  |  | 1
FIDUCIAL |  | FD3 |  | FIDUCIAL-1X2 |  | ZMBo Schematic Library.SchLib | FIDUCIAL |  |  | 1
TP4 | Socket | GND_TP |  | TP-2 |  | ZMBo Schematic Library.SchLib | Socket |  |  | 1
USB-B |  | J1 |  | PN61729 |  | ZMBo Schematic Library.SchLib | USB-B |  |  | 1
FTSH-105-XX-X-DV |  | J2 |  | FTSH-105-XX-X-DV |  | Adams Altium Library.SchLib | ARM Cortex JTAG-DEBUG Header |  |  | 1
SJ | SMD solder jumper | JP1 |  | SJ |  | 3Delight.SCHLIB | SJ |  |  | 1
XAL5050-153MEB | IND 15uH 3.9A 20% | L1 |  | XAL50xx-153 |  | 3Delight.SCHLIB | XAL5050-153MEB |  |  | 1
5988170107F | LED 0805 Green | LED1 |  | LED2012120 |  | 3Delight.SCHLIB | 5988170107F |  |  | 1
OSHW_LOGO_8MILX0150-NT |  | LOGO1 |  | OSHW_8X150_NOTEXT |  | 3Delight.SCHLIB | OSHW_LOGO_8MILX0150-NT |  |  | 1
Molex 0705430003 | Molex 4 Pin Clip Connector | M1_M1 |  | 4POL254 |  | ZMBo Schematic Library.SchLib | Molex 0705430003 Alt |  |  | 1
Molex 0705430003 | Molex 4 Pin Clip Connector | M1_M2 |  | 4POL254 |  | ZMBo Schematic Library.SchLib | Molex 0705430003 Alt |  |  | 1
Molex 0705430003 | Molex 4 Pin Clip Connector | M1_M3 |  | 4POL254 |  | ZMBo Schematic Library.SchLib | Molex 0705430003 Alt |  |  | 1
Molex 0705430003 | Molex 4 Pin Clip Connector | M1_M4 |  | 4POL254 |  | ZMBo Schematic Library.SchLib | Molex 0705430003 Alt |  |  | 1
Molex 0705430003 | Molex 4 Pin Clip Connector | M2 |  | 4POL254 |  | ZMBo Schematic Library.SchLib | Molex 0705430003 Alt |  |  | 1
Molex 0705430003 | Molex 4 Pin Clip Connector | M3 |  | 4POL254 |  | ZMBo Schematic Library.SchLib | Molex 0705430003 Alt |  |  | 1
Molex 70543-03 |  | MAX1_ES1 |  | 70543-03 |  | RADMBo Schematic Library.SchLib | Molex Endstop |  |  | 1
Molex 70543-03 |  | MAX1_ES2 |  | 70543-03 |  | RADMBo Schematic Library.SchLib | Molex Endstop |  |  | 1
Molex 70543-03 |  | MAX1_ES3 |  | 70543-03 |  | RADMBo Schematic Library.SchLib | Molex Endstop |  |  | 1
Molex 70543-03 |  | MIN1_ES1 |  | 70543-03 |  | RADMBo Schematic Library.SchLib | Molex Endstop |  |  | 1
Molex 70543-03 |  | MIN1_ES2 |  | 70543-03 |  | RADMBo Schematic Library.SchLib | Molex Endstop |  |  | 1
Molex 70543-03 |  | MIN1_ES3 |  | 70543-03 |  | RADMBo Schematic Library.SchLib | Molex Endstop |  |  | 1
ERASE | Header, 2-Pin | P1 |  | HDR1X2 |  | Miscellaneous Connectors.IntLib | Header 2 |  |  | 1
Molex 70543-02 | Molex 70543-02 | P2_TR1 |  | 70543-02 |  | ZMBo Schematic Library.SchLib | Molex 70543-02 |  |  | 1
Molex 70543-02 | Molex 70543-02 | P2_TR2 |  | 70543-02 |  | ZMBo Schematic Library.SchLib | Molex 70543-02 |  |  | 1
Molex 70543-02 | Molex 70543-02 | P2_TR3 |  | 70543-02 |  | ZMBo Schematic Library.SchLib | Molex 70543-02 |  |  | 1
Molex 70543-02 | Molex 70543-02 | P2_TR4 |  | 70543-02 |  | ZMBo Schematic Library.SchLib | Molex 70543-02 |  |  | 1
Header 5X2 | Header, 5-Pin, Dual row | P3 |  | HDR2X5 |  | Miscellaneous Connectors.IntLib | Header 5X2 |  |  | 1
Header 5X2 | Header, 5-Pin, Dual row | P4 |  | HDR2X5 |  | Miscellaneous Connectors.IntLib | Header 5X2 |  |  | 1
Header 5X2 | Header, 5-Pin, Dual row | P5 |  | HDR2X5 |  | Miscellaneous Connectors.IntLib | Header 5X2 |  |  | 1
Header 5X2 | Header, 5-Pin, Dual row | P6 |  | HDR2X5 |  | Miscellaneous Connectors.IntLib | Header 5X2 |  |  | 1
NCV8402AD |  | Q1 |  | NCV8402AD-SOIC8 |  | 3Delight.SCHLIB | NCV8402AD |  |  | 1
PSMN7R0-60YS,115 | Mosfet N-channel 60V 356A 117W 9.3mOhms | Q4 |  | SOT669 |  | 3Delight.SCHLIB | PSMN7R0-60YS,115 |  |  | 1
PSMN7R0-60YS,115 | Mosfet N-channel 60V 356A 117W 9.3mOhms | Q5 |  | SOT669 |  | 3Delight.SCHLIB | PSMN7R0-60YS,115 |  |  | 1
PSMN7R0-60YS,115 | Mosfet N-channel 60V 356A 117W 9.3mOhms | Q6 |  | SOT669 |  | 3Delight.SCHLIB | PSMN7R0-60YS,115 |  |  | 1
PSMN7R0-60YS,115 | Mosfet N-channel 60V 356A 117W 9.3mOhms | Q7 |  | SOT669 |  | 3Delight.SCHLIB | PSMN7R0-60YS,115 |  |  | 1
10K | RES 0603 10K 100mW 1% | R1 |  | R0603 |  | 3Delight.SCHLIB | ERJ-3EKF1002V |  |  | 1
2.7K | RES SMD 2.7K OHM 5% 1/10W 0402 | R2_ES1 | P2.7KJCT-ND | R0402 |  | Tigershark3D.SchLib | ERJ-2GEJ272X |  |  | 1
2.7K | RES SMD 2.7K OHM 5% 1/10W 0402 | R2_ES2 | P2.7KJCT-ND | R0402 |  | Tigershark3D.SchLib | ERJ-2GEJ272X |  |  | 1
2.7K | RES SMD 2.7K OHM 5% 1/10W 0402 | R2_ES3 | P2.7KJCT-ND | R0402 |  | Tigershark3D.SchLib | ERJ-2GEJ272X |  |  | 1
2.7K | RES SMD 2.7K OHM 5% 1/10W 0402 | R3_ES1 | P2.7KJCT-ND | R0402 |  | Tigershark3D.SchLib | ERJ-2GEJ272X |  |  | 1
2.7K | RES SMD 2.7K OHM 5% 1/10W 0402 | R3_ES2 | P2.7KJCT-ND | R0402 |  | Tigershark3D.SchLib | ERJ-2GEJ272X |  |  | 1
2.7K | RES SMD 2.7K OHM 5% 1/10W 0402 | R3_ES3 | P2.7KJCT-ND | R0402 |  | Tigershark3D.SchLib | ERJ-2GEJ272X |  |  | 1
0603 | Resistor | R4 |  | J1-0603 |  | Miscellaneous Devices.IntLib | Res3 |  |  | 1
39r | RES SMD 39 OHM 1% 1/10W 0402 | R5 |  | R0402 | 0.4mm | Tigershark3D.SchLib | ERJ-2RKF39R0X | Panasonic |  | 1
100K | RES 100K OHM 1/10W 1% 0603 SMD | R6 |  | R0603 |  | Tigershark3D.SchLib | RC0603FR-07100KL |  |  | 1
10K | RES 0603 10K 100mW 1% | R7 |  | R0603 |  | 3Delight.SCHLIB | ERJ-3EKF1002V |  |  | 1
2.7K | RES SMD 2.7K OHM 1% 1/10W 0402 | R8_M1 |  | R0402 |  | Tigershark3D.SchLib | ERJ-2RKF2701X | Panasonic |  | 1
2.7K | RES SMD 2.7K OHM 1% 1/10W 0402 | R8_M2 |  | R0402 |  | Tigershark3D.SchLib | ERJ-2RKF2701X | Panasonic |  | 1
2.7K | RES SMD 2.7K OHM 1% 1/10W 0402 | R8_M3 |  | R0402 |  | Tigershark3D.SchLib | ERJ-2RKF2701X | Panasonic |  | 1
2.7K | RES SMD 2.7K OHM 1% 1/10W 0402 | R8_M4 |  | R0402 |  | Tigershark3D.SchLib | ERJ-2RKF2701X | Panasonic |  | 1
0.6r | RES 0.06 OHM 1W 1% 2512 SMD | R9 |  | 2512R-0.55 |  | 3Delight.SCHLIB | RL2512FK-070R06L |  |  | 1
10K | RES 0603 10K 100mW 1% | R10 |  | R0603 |  | 3Delight.SCHLIB | ERJ-3EKF1002V |  |  | 1
1K | RES 0603 1K 100mW 1% | R11 |  | R0603 |  | Tigershark3D.SchLib | ERJ-3EKF1001V |  |  | 1
10K | RES 0603 10K 100mW 1% | R12 |  | R0603 |  | 3Delight.SCHLIB | ERJ-3EKF1002V |  |  | 1
1.8K | RES 0603 1.8K 100mW 5% | R13 |  | R0603 |  | Tigershark3D.SchLib | RC0603JR-071K8L |  |  | 1
4.7K | RES 0603 4.7K 100mW 1% | R14_TR1 |  | R0603 |  | 3Delight.SCHLIB | ERJ3EKF4701V |  |  | 1
4.7K | RES 0603 4.7K 100mW 1% | R14_TR2 |  | R0603 |  | 3Delight.SCHLIB | ERJ3EKF4701V |  |  | 1
4.7K | RES 0603 4.7K 100mW 1% | R14_TR3 |  | R0603 |  | 3Delight.SCHLIB | ERJ3EKF4701V |  |  | 1
4.7K | RES 0603 4.7K 100mW 1% | R14_TR4 |  | R0603 |  | 3Delight.SCHLIB | ERJ3EKF4701V |  |  | 1
24r | RES SMD 24 OHM 1% 1/10W 0603 | R15 |  | R0603 |  | Tigershark3D.SchLib | RC1608F240CS | Samsung |  | 1
24r | RES SMD 24 OHM 1% 1/10W 0603 | R16 |  | R0603 |  | Tigershark3D.SchLib | RC1608F240CS | Samsung |  | 1
200K | RES 0402 22r 63mW 1% | R17 |  | R0402 |  | 3Delight.SCHLIB | CRCW0402200KFKED |  |  | 1
24r | RES SMD 24 OHM 1% 1/10W 0603 | R18 |  | R0603 |  | Tigershark3D.SchLib | RC1608F240CS | Samsung |  | 1
4.7K | RES 0603 4.7K 100mW 1% | R19_TR1 |  | R0603 |  | 3Delight.SCHLIB | ERJ3EKF4701V |  |  | 1
4.7K | RES 0603 4.7K 100mW 1% | R19_TR2 |  | R0603 |  | 3Delight.SCHLIB | ERJ3EKF4701V |  |  | 1
4.7K | RES 0603 4.7K 100mW 1% | R19_TR3 |  | R0603 |  | 3Delight.SCHLIB | ERJ3EKF4701V |  |  | 1
4.7K | RES 0603 4.7K 100mW 1% | R19_TR4 |  | R0603 |  | 3Delight.SCHLIB | ERJ3EKF4701V |  |  | 1
24r | RES SMD 24 OHM 1% 1/10W 0603 | R20 |  | R0603 |  | Tigershark3D.SchLib | RC1608F240CS | Samsung |  | 1
10K | RES 0603 10K 100mW 1% | R21 |  | R0603 |  | 3Delight.SCHLIB | ERJ-3EKF1002V |  |  | 1
39r | RES SMD 39 OHM 1% 1/10W 0402 | R22 |  | R0402 | 0.4mm | Tigershark3D.SchLib | ERJ-2RKF39R0X | Panasonic |  | 1
6.8K | RES SMD 6.8K OHM 1% 1/16W 0402 | R23 |  | R0402 | 0.4mm | Tigershark3D.SchLib | CRCW04026K80FKED | Vishay Dale |  | 1
1M | RES 0402 1M 100mW 5% | R24 |  | R0402 |  | Tigershark3D.SchLib | ERJ2GEJ105X |  |  | 1
1K | RES 0603 1K 100mW 1% | R25 |  | R0603 |  | Tigershark3D.SchLib | ERJ-3EKF1001V |  |  | 1
1K | RES 0603 1K 100mW 1% | R26 |  | R0603 |  | Tigershark3D.SchLib | ERJ-3EKF1001V |  |  | 1
2.7K | RES SMD 2.7K OHM 1% 1/10W 0402 | R27 |  | R0402 |  | Tigershark3D.SchLib | ERJ-2RKF2701X | Panasonic |  | 1
10K | RES 0603 10K 100mW 1% | R28 |  | R0603 |  | Tigershark3D.SchLib | ERJ-3EKF1002V |  |  | 1
10K | RES 0603 10K 100mW 1% | R29 |  | R0603 |  | Tigershark3D.SchLib | ERJ-3EKF1002V |  |  | 1
1M | RES 0402 1M 100mW 5% | R30_M1 |  | R0402 |  | Tigershark3D.SchLib | ERJ2GEJ105X |  |  | 1
1M | RES 0402 1M 100mW 5% | R30_M2 |  | R0402 |  | Tigershark3D.SchLib | ERJ2GEJ105X |  |  | 1
1M | RES 0402 1M 100mW 5% | R30_M3 |  | R0402 |  | Tigershark3D.SchLib | ERJ2GEJ105X |  |  | 1
1M | RES 0402 1M 100mW 5% | R30_M4 |  | R0402 |  | Tigershark3D.SchLib | ERJ2GEJ105X |  |  | 1
2.7K | RES SMD 2.7K OHM 1% 1/10W 0402 | R31_M1 |  | R0402 |  | Tigershark3D.SchLib | ERJ-2RKF2701X | Panasonic |  | 1
2.7K | RES SMD 2.7K OHM 1% 1/10W 0402 | R31_M2 |  | R0402 |  | Tigershark3D.SchLib | ERJ-2RKF2701X | Panasonic |  | 1
2.7K | RES SMD 2.7K OHM 1% 1/10W 0402 | R31_M3 |  | R0402 |  | Tigershark3D.SchLib | ERJ-2RKF2701X | Panasonic |  | 1
2.7K | RES SMD 2.7K OHM 1% 1/10W 0402 | R31_M4 |  | R0402 |  | Tigershark3D.SchLib | ERJ-2RKF2701X | Panasonic |  | 1
2512 | RES SMD 0.1 OHM 1% 2W 2512 | R32_M1 | CSRN2512FTR100TR-ND | 2512R-0.55 |  | Tigershark3D.SchLib | CSRN2512FTR100 |  | Stackpole ELectronics Inc | 1
2512 | RES SMD 0.1 OHM 1% 2W 2512 | R32_M2 | CSRN2512FTR100TR-ND | 2512R-0.55 |  | Tigershark3D.SchLib | CSRN2512FTR100 |  | Stackpole ELectronics Inc | 1
2512 | RES SMD 0.1 OHM 1% 2W 2512 | R32_M3 | CSRN2512FTR100TR-ND | 2512R-0.55 |  | Tigershark3D.SchLib | CSRN2512FTR100 |  | Stackpole ELectronics Inc | 1
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

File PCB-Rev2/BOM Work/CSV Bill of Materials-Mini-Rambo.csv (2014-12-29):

Comment | Description | Designator | Footprint | LibRef | Quantity
PCB | PCB |  |  | PCB | 1
22pF | CAP CER 0402 22pF 50V 5% C0G | C1 | C0402 | 04025A220JAT2A | 1
10uF | CAP CER 0805 10uF 10V 10% X5R | C2 | C0805 | C0805C106K8PACTU | 1
100nF | CAP CER 0603 100nF 50V 10% X7R | C3 | C0603 | C0603C104K5RACTU | 1
100nF | CAP CER 0402 100nF 16V 10% X7R | C4 | C0402 | GRM155R71C104KA88D | 1
470uF | CAP ALU 470uF 50V 20% | C5 | C12,5-5 | UPW1H471MHD1TO | 1
100nF | CAP CER 0402 100nF 16V 10% X7R | C6 | C0402 | GRM155R71C104KA88D | 1
100nF | CAP CER 0402 100nF 16V 10% X7R | C7 | C0402 | GRM155R71C104KA88D | 1
100nF | CAP CER 0402 100nF 16V 10% X7R | C8 | C0402 | GRM155R71C104KA88D | 1
100nF | CAP CER 0402 100nF 16V 10% X7R | C9 | C0402 | GRM155R71C104KA88D | 1
100nF | CAP CER 0402 100nF 16V 10% X7R | C10 | C0402 | GRM155R71C104KA88D | 1
100nF | CAP CER 0402 100nF 16V 10% X7R | C11 | C0402 | GRM155R71C104KA88D | 1
22pF | CAP CER 0402 22pF 50V 5% C0G | C12 | C0402 | 04025A220JAT2A | 1
22pF | CAP CER 0402 22pF 50V 5% C0G | C13 | C0402 | 04025A220JAT2A | 1
100nF | CAP CER 0402 100nF 16V 10% X7R | C14 | C0402 | GRM155R71C104KA88D | 1
100nF | CAP CER 0402 100nF 16V 10% X7R | C15 | C0402 | GRM155R71C104KA88D | 1
1uF | CAP CER 0402 1uF 6.3V 10% X5R | C16 | C0402 | GRM155R60J105KE19D | 1
100nF | CAP CER 0603 100nF 50V 10% X7R | C17 | C0603 | C0603C104K5RACTU | 1
100nF | CAP CER 0603 100nF 50V 10% X7R | C18 | C0603 | C0603C104K5RACTU | 1
1uF | CAP CER 0402 1uF 6.3V 10% X5R | C19 | C0402 | GRM155R60J105KE19D | 1
1uF | CAP CER 0402 1uF 6.3V 10% X5R | C20 | C0402 | GRM155R60J105KE19D | 1
1uF | CAP CER 0402 1uF 6.3V 10% X5R | C21 | C0402 | GRM155R60J105KE19D | 1
1uF | CAP CER 0402 1uF 6.3V 10% X5R | C22 | C0402 | GRM155R60J105KE19D | 1
100nF | CAP CER 0603 100nF 50V 10% X7R | C23 | C0603 | C0603C104K5RACTU | 1
100nF | CAP CER 0603 100nF 50V 10% X7R | C24 | C0603 | C0603C104K5RACTU | 1
100nF | CAP CER 0603 100nF 50V 10% X7R | C25 | C0603 | C0603C104K5RACTU | 1
100nF | CAP CER 0402 100nF 16V 10% X7R | C26 | C0402 | GRM155R71C104KA88D | 1
100nF | CAP CER 0603 100nF 50V 10% X7R | C27 | C0603 | C0603C104K5RACTU | 1
100nF | CAP CER 0603 100nF 50V 10% X7R | C28 | C0603 | C0603C104K5RACTU | 1
100nF | CAP CER 0603 100nF 50V 10% X7R | C29 | C0603 | C0603C104K5RACTU | 1
4.7uF | CAP CER 1206 4.7uF 50V 10% X5R | C30 | C1206 | C1206C475K5PACTU | 1
220nF | CAP CER 0603 220nF 10V 10% X7R | C31 | C0603 | CC0603KRX7R7BB224 | 1
100nF | CAP CER 0603 100nF 50V 10% X7R | C32 | C0603 | C0603C104K5RACTU | 1
100nF | CAP CER 0603 100nF 50V 10% X7R | C33 | C0603 | C0603C104K5RACTU | 1
100nF | CAP CER 0603 100nF 50V 10% X7R | C34 | C0603 | C0603C104K5RACTU | 1
1uF | CAP CER 0805 1uF 50V 10% X7R | C35 | C0805 | GRM21BR71H105KA12L | 1
220nF | CAP CER 0603 220nF 10V 10% X7R | C36 | C0603 | CC0603KRX7R7BB224 | 1
100nF | CAP CER 0603 100nF 50V 10% X7R | C37 | C0603 | C0603C104K5RACTU | 1
100nF | CAP CER 0603 100nF 50V 10% X7R | C38 | C0603 | C0603C104K5RACTU | 1
100nF | CAP CER 0603 100nF 50V 10% X7R | C39 | C0603 | C0603C104K5RACTU | 1
100nF | CAP CER 0603 100nF 50V 10% X7R | C40 | C0603 | C0603C104K5RACTU | 1
220nF | CAP CER 0603 220nF 10V 10% X7R | C41 | C0603 | CC0603KRX7R7BB224 | 1
100nF | CAP CER 0603 100nF 50V 10% X7R | C42 | C0603 | C0603C104K5RACTU | 1
100nF | CAP CER 0603 100nF 50V 10% X7R | C43 | C0603 | C0603C104K5RACTU | 1
100nF | CAP CER 0603 100nF 50V 10% X7R | C44 | C0603 | C0603C104K5RACTU | 1
10uF | CAP CER 0805 10uF 10V 10% X5R | C45 | C0805 | C0805C106K8PACTU | 1
220nF | CAP CER 0603 220nF 10V 10% X7R | C46 | C0603 | CC0603KRX7R7BB224 | 1
1uF | CAP CER 0402 1uF 6.3V 10% X5R | C47 | C0402 | GRM155R60J105KE19D | 1
1uF | CAP CER 0402 1uF 6.3V 10% X5R | C48 | C0402 | GRM155R60J105KE19D | 1
1uF | CAP CER 0402 1uF 6.3V 10% X5R | C49 | C0402 | GRM155R60J105KE19D | 1
100nF | CAP CER 0402 100nF 16V 10% X7R | C52 | C0402 | GRM155R71C104KA88D | 1
100uF | CAP ALU 100uF 50V 20% 105C | C53 | C3,5-8 | UVZ1H101MPD1TD | 1
100uF | CAP ALU 100uF 50V 20% 105C | C54 | C3,5-8 | UVZ1H101MPD1TD | 1
100nF | CAP CER 0402 100nF 16V 10% X7R | C56 | C0402 | GRM155R71C104KA88D | 1
22pF | CAP CER 0402 22pF 50V 5% C0G | C57 | C0402 | 04025A220JAT2A | 1
22pF | CAP CER 0402 22pF 50V 5% C0G | C58 | C0402 | 04025A220JAT2A | 1
100nF | CAP CER 0402 100nF 16V 10% X7R | C59 | C0402 | GRM155R71C104KA88D | 1
100nF | CAP CER 0603 100nF 50V 10% X7R | C60 | C0603 | C0603C104K5RACTU | 1
100nF | CAP CER 0603 100nF 50V 10% X7R | C62 | C0603 | C0603C104K5RACTU | 1
4.7nF | CAP CER 0402 4.7nF 25V 10% X7R | C63 | C0402 | CC0402KRX7R8BB472 | 1
100nF | CAP CER 0402 100nF 16V 10% X7R | C67 | C0402 | GRM155R71C104KA88D | 1
100nF | CAP CER 0402 100nF 16V 10% X7R | C68 | C0402 | GRM155R71C104KA88D | 1
100nF | CAP CER 0402 100nF 16V 10% X7R | C69 | C0402 | GRM155R71C104KA88D | 1
100nF | CAP CER 0402 100nF 16V 10% X7R | C70 | C0402 | GRM155R71C104KA88D | 1
100nF | CAP CER 0603 100nF 50V 10% X7R | C71 | C0603 | C0603C104K5RACTU | 1
100nF | CAP CER 0603 100nF 50V 10% X7R | C72 | C0603 | C0603C104K5RACTU | 1
100nF | CAP CER 0603 100nF 50V 10% X7R | C73 | C0603 | C0603C104K5RACTU | 1
100nF | CAP CER 0603 100nF 50V 10% X7R | C74 | C0603 | C0603C104K5RACTU | 1
1N4148WT | DIODE SOD523 | D1 | SOD523 | 1N4148WT | 1
SMAJ30A | DIODE TVS 30V SMA | D2 | SMA-SM | SMAJ30A | 1
1N4148WT | DIODE SOD523 | D3 | SOD523 | 1N4148WT | 1
1N4148WT | DIODE SOD523 | D4 | SOD523 | 1N4148WT | 1
1N4148WT | DIODE SOD523 | D5 | SOD523 | 1N4148WT | 1
SK310A-TP | DIODE Schottky 3A SMA | D6 | SMA-SM | SK310A | 1
S3A-13-F | DIODE DO-214AB | D7 | DO-214AB | S3A-13-F | 1
SMAJ30A | DIODE TVS 30V SMA | D8 | SMA-SM | SMAJ30A | 1
SK310A-TP | DIODE Schottky 3A SMA | D9 | SMA-SM | SK310A | 1
SK310A-TP | DIODE Schottky 3A SMA | D10 | SMA-SM | SK310A | 1
1N4148WT | DIODE SOD523 | D11 | SOD523 | 1N4148WT | 1
SZMM3Z4V7T1G | Z-Diode | D12 | SOD323-R | ZENER-DIODE | 1
1N4148WT | DIODE SOD523 | D13 | SOD523 | 1N4148WT | 1
1N4148WT | DIODE SOD523 | D14 | SOD523 | 1N4148WT | 1
1N4148WT | DIODE SOD523 | D15 | SOD523 | 1N4148WT | 1
RSB39VTE-17 | DIODE TVS | D16 | SOD323-R | RSB39VTE-17 | 1
3522-2 | FUSE PTH ATO | F1 | 3522-2 | 3522-2 | 1
3522-2 | FUSE PTH ATO | F2 | 3522-2 | 3522-2 | 1
3522-2 | FUSE PTH ATO | F3 | 3522-2 | 3522-2 | 1
PTS181233V075 | FUSE 1812 PTC 750mA 6V | F5 | PTS1812 Fuse | PTS181233V075 | 1
BLM41PG600SN1L | FERRITE BEAD 1806 60ohm | FB1 | L1806 | BLM41PG600SN1L | 1
BLM41PG600SN1L | FERRITE BEAD 1806 60ohm | FB2 | L1806 | BLM41PG600SN1L | 1
FIDUCIAL | Fiducial | FID1 | FIDUCIAL-1X2 | FIDUCIAL | 1
FIDUCIAL | Fiducial | FID2 | FIDUCIAL-1X2 | FIDUCIAL | 1
FIDUCIAL | Fiducial | FID3 | FIDUCIAL-1X2 | FIDUCIAL | 1
XAL5050-153MED | IND 15uH 3.9A 20% | L1 | XAL50xx-153 | XAL5050-153MED | 1
CBC2012T100M | IND 0805 10uH 240mA 20% | L2 | C0805 | CBC2012T100M | 1
5988140107F | LED 0805 Yellow | LED1 | LED2012120 | 5988140107F | 1
5988110107F | LED 0805 Red | LED2 | LED2012120 | 5988110107F | 1
5988110107F | LED 0805 Red | LED3 | LED2012120 | 5988110107F | 1
5988140107F | LED 0805 Yellow | LED4 | LED2012120 | 5988140107F | 1
5988110107F | LED 0805 Red | LED6 | LED2012120 | 5988110107F | 1
5988170107F | LED 0805 Green | LED7 | LED2012120 | 5988170107F | 1
5988110107F | LED 0805 Red | LED8 | LED2012120 | 5988110107F | 1
5988140107F | LED 0805 Yellow | LED10 | LED2012120 | 5988140107F | 1
5-104068-1 | HDR 20pos Vert Dual Row | P1 | 10X2-0.05X0.1w | 5-104068-1 | 1
5-104068-1 | HDR 20pos Vert Dual Row | P2 | 10X2-0.05X0.1w | 5-104068-1 | 1
5x2 IDCw |  | P3 | 2x5 IDCw | 5X2 IDCw | 1
PSMN7R0-60YS,115 | Mosfet N-channel 60V 356A 117W 9.3mOhms | Q1 | SOT669 | PSMN7R0-60YS,115 | 1
PSMN7R0-60YS,115 | Mosfet N-channel 60V 356A 117W 9.3mOhms | Q5 | SOT669 | PSMN7R0-60YS,115 | 1
IRLML6346TRPBF | Mosfet N-Channel 30V 3.4A 63mOhm | Q8 | SOT23-3 | IRLML6346TRPBF | 1
IRLML6346TRPBF | Mosfet N-Channel 30V 3.4A 63mOhm | Q9 | SOT23-3 | IRLML6346TRPBF | 1
22r | RES 0402 22r 62.5mW 1% | R1 | R0402 | RC0402FR-0722RL | 1
22r | RES 0402 22r 62.5mW 1% | R2 | R0402 | RC0402FR-0722RL | 1
200K | RES 0402 22r 63mW 1% | R3 | R0402 | CRCW0402200KFKED | 1
0.1r | RES 1206 0.1r 0.5w 1% | R4 | R1206 | CRM1206-FX-R100ELF | 1
4.7K | RES 0603 4.7K 100mW 1% | R5 | R0603 | ERJ3EKF4701V | 1
4.7K | RES 0603 4.7K 100mW 1% | R6 | R0603 | ERJ3EKF4701V | 1
0.1r | RES 1206 0.1r 0.5w 1% | R7 | R1206 | CRM1206-FX-R100ELF | 1
0.1r | RES 1206 0.1r 0.5w 1% | R8 | R1206 | CRM1206-FX-R100ELF | 1
10r | RES 0603 10r 100mW 1% | R9 | R0603 | CRCW060310R0FKEA | 1
0.1r | RES 1206 0.1r 0.5w 1% | R10 | R1206 | CRM1206-FX-R100ELF | 1
10K | RES 0603 10K 100mW 1% | R11 | R0603 | ERJ-3EKF1002V | 1
0.6r | RES 0.06 OHM 1W 1% 2512 SMD | R13 | 2512R-0.55 | RL2512FK-070R06L | 1
0.1r | RES 1206 0.1r 0.5w 1% | R14 | R1206 | CRM1206-FX-R100ELF | 1
0.1r | RES 1206 0.1r 0.5w 1% | R15 | R1206 | CRM1206-FX-R100ELF | 1
100K | RES 100K OHM 1/10W 1% 0603 SMD | R16 | R0603 | RC0603FR-07100KL | 1
0.1r | RES 1206 0.1r 0.5w 1% | R19 | R1206 | CRM1206-FX-R100ELF | 1
0.1r | RES 1206 0.1r 0.5w 1% | R20 | R1206 | CRM1206-FX-R100ELF | 1
100K | RES 100K OHM 1/10W 1% 0603 SMD | R21 | R0603 | RC0603FR-07100KL | 1
10K | RES 0603 10K 100mW 1% | R23 | R0603 | ERJ-3EKF1002V | 1
10K | RES 0603 10K 100mW 1% | R24 | R0603 | ERJ-3EKF1002V | 1
4.7K | RES 0603 4.7K 100mW 1% | R31 | R0603 | ERJ3EKF4701V | 1
4.7K | RES 0603 4.7K 100mW 1% | R32 | R0603 | ERJ3EKF4701V | 1
1K | RES 0603 1K 100mW 1% | R33 | R0603 | ERJ-3EKF1001V | 1
1K | RES 0603 1K 100mW 1% | R34 | R0603 | ERJ-3EKF1001V | 1
1K | RES 0603 1K 100mW 1% | R35 | R0603 | ERJ-3EKF1001V | 1
4.7K | RES 0603 4.7K 100mW 1% | R36 | R0603 | ERJ3EKF4701V | 1
4.7K | RES 0603 4.7K 100mW 1% | R37 | R0603 | ERJ3EKF4701V | 1
1.8K | RES 0603 1.8K 100mW 5% | R40 | R0603 | RC0603JR-071K8L | 1
10r | RES 0603 10r 100mW 1% | R42 | R0603 | CRCW060310R0FKEA | 1
100K | RES 100K OHM 1/10W 1% 0603 SMD | R43 | R0603 | RC0603FR-07100KL | 1
10K | RES 0603 10K 100mW 1% | R46 | R0603 | ERJ-3EKF1002V | 1
10K | RES 0603 10K 100mW 1% | R47 | R0603 | ERJ-3EKF1002V | 1
10r | RES 0603 10r 100mW 1% | R56 | R0603 | CRCW060310R0FKEA | 1
100K | RES 100K OHM 1/10W 1% 0603 SMD | R57 | R0603 | RC0603FR-07100KL | 1
1.8K | RES 0603 1.8K 100mW 5% | R58 | R0603 | RC0603JR-071K8L | 1
100K | RES 100K OHM 1/10W 1% 0603 SMD | R59 | R0603 | RC0603FR-07100KL | 1
100K | RES 100K OHM 1/10W 1% 0603 SMD | R60 | R0603 | RC0603FR-07100KL | 1
100K | RES 100K OHM 1/10W 1% 0603 SMD | R61 | R0603 | RC0603FR-07100KL | 1
100K | RES 100K OHM 1/10W 1% 0603 SMD | R62 | R0603 | RC0603FR-07100KL | 1
1.8K | RES 0603 1.8K 100mW 5% | R69 | R0603 | RC0603JR-071K8L | 1
1.8K | RES 0603 1.8K 100mW 5% | R70 | R0603 | RC0603JR-071K8L | 1
10r | RES 0603 10r 100mW 1% | R71 | R0603 | CRCW060310R0FKEA | 1
1M | RES 0402 1M 100mW 5% | R72 | R0402 | ERJ2GEJ105X | 1
10K | RES 0603 10K 100mW 1% | R73 | R0603 | ERJ-3EKF1002V | 1
10K | RES ARRAY 4 RES 10K 1206 62.5mW 5% | RN1 | CAY16 | CAY16-103J4LF | 1
10K | RES ARRAY 4 RES 10K 1206 62.5mW 5% | RN2 | CAY16 | CAY16-103J4LF | 1
10K | RES ARRAY 4 RES 10K 1206 62.5mW 5% | RN3 | CAY16 | CAY16-103J4LF | 1
1K | RES ARRAY 4 RES 1K 1206 62.5mW 5% | RN5 | CAY16 | CAY16-102J4LF | 1
CG0603MLC-05E | VAR 0603 5V | RV1 | R0603 | CG0603MLC-05E | 1
CG0603MLC-05E | VAR 0603 5V | RV2 | R0603 | CG0603MLC-05E | 1
1571610-2 | SWTCH Momentary Washable | S1 | B3F-31XX | 1571610-2 | 1
TestPoint | Test Point | TP3 | TP1-27 | TestPoint | 1
TestPoint | Test Point | TP16 | TP1-27 | TestPoint | 1
TestPoint | Test Point | TP17 | TP1-27 | TestPoint | 1
TestPoint | Test Point | TP18 | TP1-27 | TestPoint | 1
TestPoint | Test Point | TP22 | TP1-27 | TestPoint | 1
TestPoint | Test Point | TP23 | TP1-27 | TestPoint | 1
TestPoint | Test Point | TP24 | TP1-27 | TestPoint | 1
TestPoint | Test Point | TP25 | TP1-27 | TestPoint | 1
TestPoint | Test Point | TP26 | TP1-27 | TestPoint | 1
TestPoint | Test Point | TP27 | TP1-27 | TestPoint | 1
TestPoint | Test Point | TP28 | TP1-27 | TestPoint | 1
TestPoint | Test Point | TP29 | TP1-27 | TestPoint | 1
TestPoint | Test Point | TP30 | TP1-27 | TestPoint | 1
TestPoint | Test Point | TP31 | TP1-27 | TestPoint | 1
TestPoint | Test Point | TP32 | TP1-27 | TestPoint | 1
TestPoint | Test Point | TP33 | TP1-27 | TestPoint | 1
TestPoint | Test Point | TP34 | TP1-27 | TestPoint | 1
TestPoint | Test Point | TP35 | TP1-27 | TestPoint | 1
TestPoint | Test Point | TP36 | TP1-27 | TestPoint | 1
TestPoint | Test Point | TP37 | TP1-27 | TestPoint | 1
TestPoint | Test Point | TP38 | TP1-27 | TestPoint | 1
TestPoint | Test Point | TP39 | TP1-27 | TestPoint | 1
TestPoint | Test Point | TP40 | TP1-27 | TestPoint | 1
TestPoint | Test Point | TP41 | TP1-27 | TestPoint | 1
TestPoint | Test Point | TP42 | TP1-27 | TestPoint | 1
TestPoint | Test Point | TP43 | TP1-27 | TestPoint | 1
TestPoint | Test Point | TP44 | TP1-27 | TestPoint | 1
TestPoint | Test Point | TP45 | TP1-27 | TestPoint | 1
TestPoint | Test Point | TP46 | TP1-27 | TestPoint | 1
TestPoint | Test Point | TP47 | TP1-27 | TestPoint | 1
TestPoint | Test Point | TP48 | TP1-27 | TestPoint | 1
TestPoint | Test Point | TP49 | TP1-27 | TestPoint | 1
TestPoint | Test Point | TP50 | TP1-27 | TestPoint | 1
TestPoint | Test Point | TP51 | TP1-27 | TestPoint | 1
TestPoint | Test Point | TP52 | TP1-27 | TestPoint | 1
TestPoint | Test Point | TP53 | TP1-27 | TestPoint | 1
TestPoint | Test Point | TP54 | TP1-27 | TestPoint | 1
TestPoint | Test Point | TP55 | TP1-27 | TestPoint | 1
TestPoint | Test Point | TP56 | TP1-27 | TestPoint | 1
TestPoint | Test Point | TP57 | TP1-27 | TestPoint | 1
TestPoint | Test Point | TP58 | TP1-27 | TestPoint | 1
TestPoint | Test Point | TP59 | TP1-27 | TestPoint | 1
TestPoint | Test Point | TP60 | TP1-27 | TestPoint | 1
TestPoint | Test Point | TP61 | TP1-27 | TestPoint | 1
TestPoint | Test Point | TP62 | TP1-27 | TestPoint | 1
TestPoint | Test Point | TP63 | TP1-27 | TestPoint | 1
TestPoint | Test Point | TP64 | TP1-27 | TestPoint | 1
TestPoint | Test Point | TP65 | TP1-27 | TestPoint | 1
TestPoint | Test Point | TP66 | TP1-27 | TestPoint | 1
TestPoint | Test Point | TP67 | TP1-27 | TestPoint | 1
TestPoint | Test Point | TP68 | TP1-27 | TestPoint | 1
TestPoint | Test Point | TP69 | TP1-27 | TestPoint | 1
Atmega32u2 | Atmega32u2 | U1 | QFN32_050050 | ATMEGA32U2-MU2 | 1
Atmega2560 | Atmega2560 | U2 | TQFP100_140140_012 | ATMEGA2560AU | 1
LM25011MY/NOPB | REG BUCK | U3 | VSSOP10 | LM25011 | 1
A4982 | Stepper Driver - Fully Integrated, Control and Power Stage | U5 | QFN32_050050 | A4982QFN32 | 1
A4982 | Stepper Driver - Fully Integrated, Control and Power Stage | U6 | QFN32_050050 | A4982QFN32 | 1
A4982 | Stepper Driver - Fully Integrated, Control and Power Stage | U7 | QFN32_050050 | A4982QFN32 | 1
A4982 | Stepper Driver - Fully Integrated, Control and Power Stage | U8 | QFN32_050050 | A4982QFN32 | 1
ADUM7441 | 4ch iCoupler | U10 | QSOP16 | ADUM7441 | 1
C-GRID-02-70543 | Connector 2pos 2.54mm locking | X1 | 70543-02 | C-GRID-02-70543 | 1
USB-B | USB connector B PTH | X2 | PN61729 | USB-B | 1
0395311004 | PHOENIX | X3 | MSTBV4 | MSTBV4 | 1
MPT4 | PHOENIX CONNECTOR | X4 | 4POL254 | MPT4 | 1
C-GRID-03-70543 | Connector 2pos 2.54mm locking | X5 | 70543-03 | C-GRID-03-70543 | 1
MPT4 | PHOENIX CONNECTOR | X6 | 4POL254 | MPT4 | 1
C-GRID-03-70543 | Connector 2pos 2.54mm locking | X7 | 70543-03 | C-GRID-03-70543 | 1
MPT4 | PHOENIX CONNECTOR | X8 | 4POL254 | MPT4 | 1
C-GRID-02-70543 | Connector 2pos 2.54mm locking | X9 | 70543-02 | C-GRID-02-70543 | 1
0395311004 | PHOENIX | X10 | MSTBV4 | MSTBV4 | 1
C-GRID-03-70543 | Connector 2pos 2.54mm locking | X11 | 70543-03 | C-GRID-03-70543 | 1
C-GRID-02-70543 | Connector 2pos 2.54mm locking | X12 | 70543-02 | C-GRID-02-70543 | 1
MPT4 | PHOENIX CONNECTOR | X14 | 4POL254 noPol | MPT4 | 1
MPT4 | PHOENIX CONNECTOR | X15 | 4POL254 noPol | MPT4 | 1
PINHD-2X3 | PIN HEADER | X17 | 2X03 | PINHD-2X3 | 1
PINHD-2X3 | PIN HEADER | X18 | 2X03 | PINHD-2X3 | 1
C-GRID-03-70543 | Connector 2pos 2.54mm locking | X21 | 70543-03 | C-GRID-03-70543 | 1
C-GRID-03-70543 | Connector 2pos 2.54mm locking | X22 | 70543-03 | C-GRID-03-70543 | 1
C-GRID-03-70543 | Connector 2pos 2.54mm locking | X23 | 70543-03 | C-GRID-03-70543 | 1
C-GRID-02-70543 | Connector 2pos 2.54mm locking | X27 | 70543-02 | C-GRID-02-70543 | 1
C-GRID-02-70543 | Connector 2pos 2.54mm locking | X28 | 70543-02 | C-GRID-02-70543 | 1
M02PTH | Connector 2x1 2.54mm PTH | X35 | 1X02 | M02PTH | 1
7M-16.000MEEQ-T | Crystal 16mHz 10ppm 10pF | Y1 | CRYS320250 | 7M-16.000MEEQ-T | 1
7M-16.000MEEQ-T | Crystal 16mHz 10ppm 10pF | Y2 | CRYS320250 | 7M-16.000MEEQ-T | 1
ATO Fuses | Description | _1 |  | Fuses | 1
ATO Fuses | Description | _2 |  | Fuses | 1
ATO Fuses | Description | _3 |  | Fuses | 1
 | Description | _A |  | PCB assembly | 1
 | Description | _AH |  | Harness assembly | 1
 | Description | _WK |  | Wire Kit | 1

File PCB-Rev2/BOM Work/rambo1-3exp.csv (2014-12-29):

Parts | Qty | Value | Package |  | Description | Manufacturer | mfr part #
C31, C36, C41, C46, C51 | 5 | 0.22uF | C0603 |  | 0.22uF 100V capacitor X or 15% | Yageo | CC0603KRX7R7BB224
C1, C12, C13, C57, C58 | 5 | 22pF | C0603-ROUND | arrow | 22pF 50V capacitor | TDK | C1608C0G1H220J
C16 | 1 | 1uF | C0603-ROUND | mouser | 1uF 10V capacitor | yageo | CC0603ZRY5V6BB105
C2 | 1 | 10uF | C0805 | arrow | 10uF | Kemet | C0805C106K8PACTU
C30 | 1 | 10uF | C1210K |  | Multilayer Ceramic Capacitors MLCC - SMD/SMT 1210 10uF 25volts X5R 10% | TDK | C3225X5R1E106K
C35, C53, C54 | 3 | 10nF | C0603 | tti | 10nF (0.01uF) 25V capacitor | TDK | C1608X7R1E103K080AA
C40 | 1 | 1uF | C0805 |  | Multilayer Ceramic Capacitors MLCC - SMD/SMT 1.0UF 50V 10% 0805ÿ | Murata | GRM21BR71H105KA12L
C45 | 1 | 10uF | C2220K | tti | 10uF | TDK | C5750X7R1H106M230KB
C6, C7, C8, C9, C10, C11, C14, C15, C26, C52, C3, C4, C17, C18, C23, C24, C27, C28, C29, C32, C33, C34, C37, C38, C39, C42, C43, C44, C47, C48, C49, C55, C56, C59, C64, C71, C72, C73, C74, C75, C25, C60, C62 | 43 | 100nF | C0603-ROUND | arrow | 0.1uF 50V capacitor | Kemet | C0603C104K5RACTU
C63 | 1 | 4.7nF | C0402 |  | Multilayer Ceramic Capacitors MLCC - SMD/SMT 4.7nF 25V X7R 10% |  | CC0402KRX7R8BB472
C67, C68, C69, C70 | 4 | 100nF | C0402 |  | CAP CER 0.1UF 16V 10% X7R 0402 |  | GRM155R71C104KA88D
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

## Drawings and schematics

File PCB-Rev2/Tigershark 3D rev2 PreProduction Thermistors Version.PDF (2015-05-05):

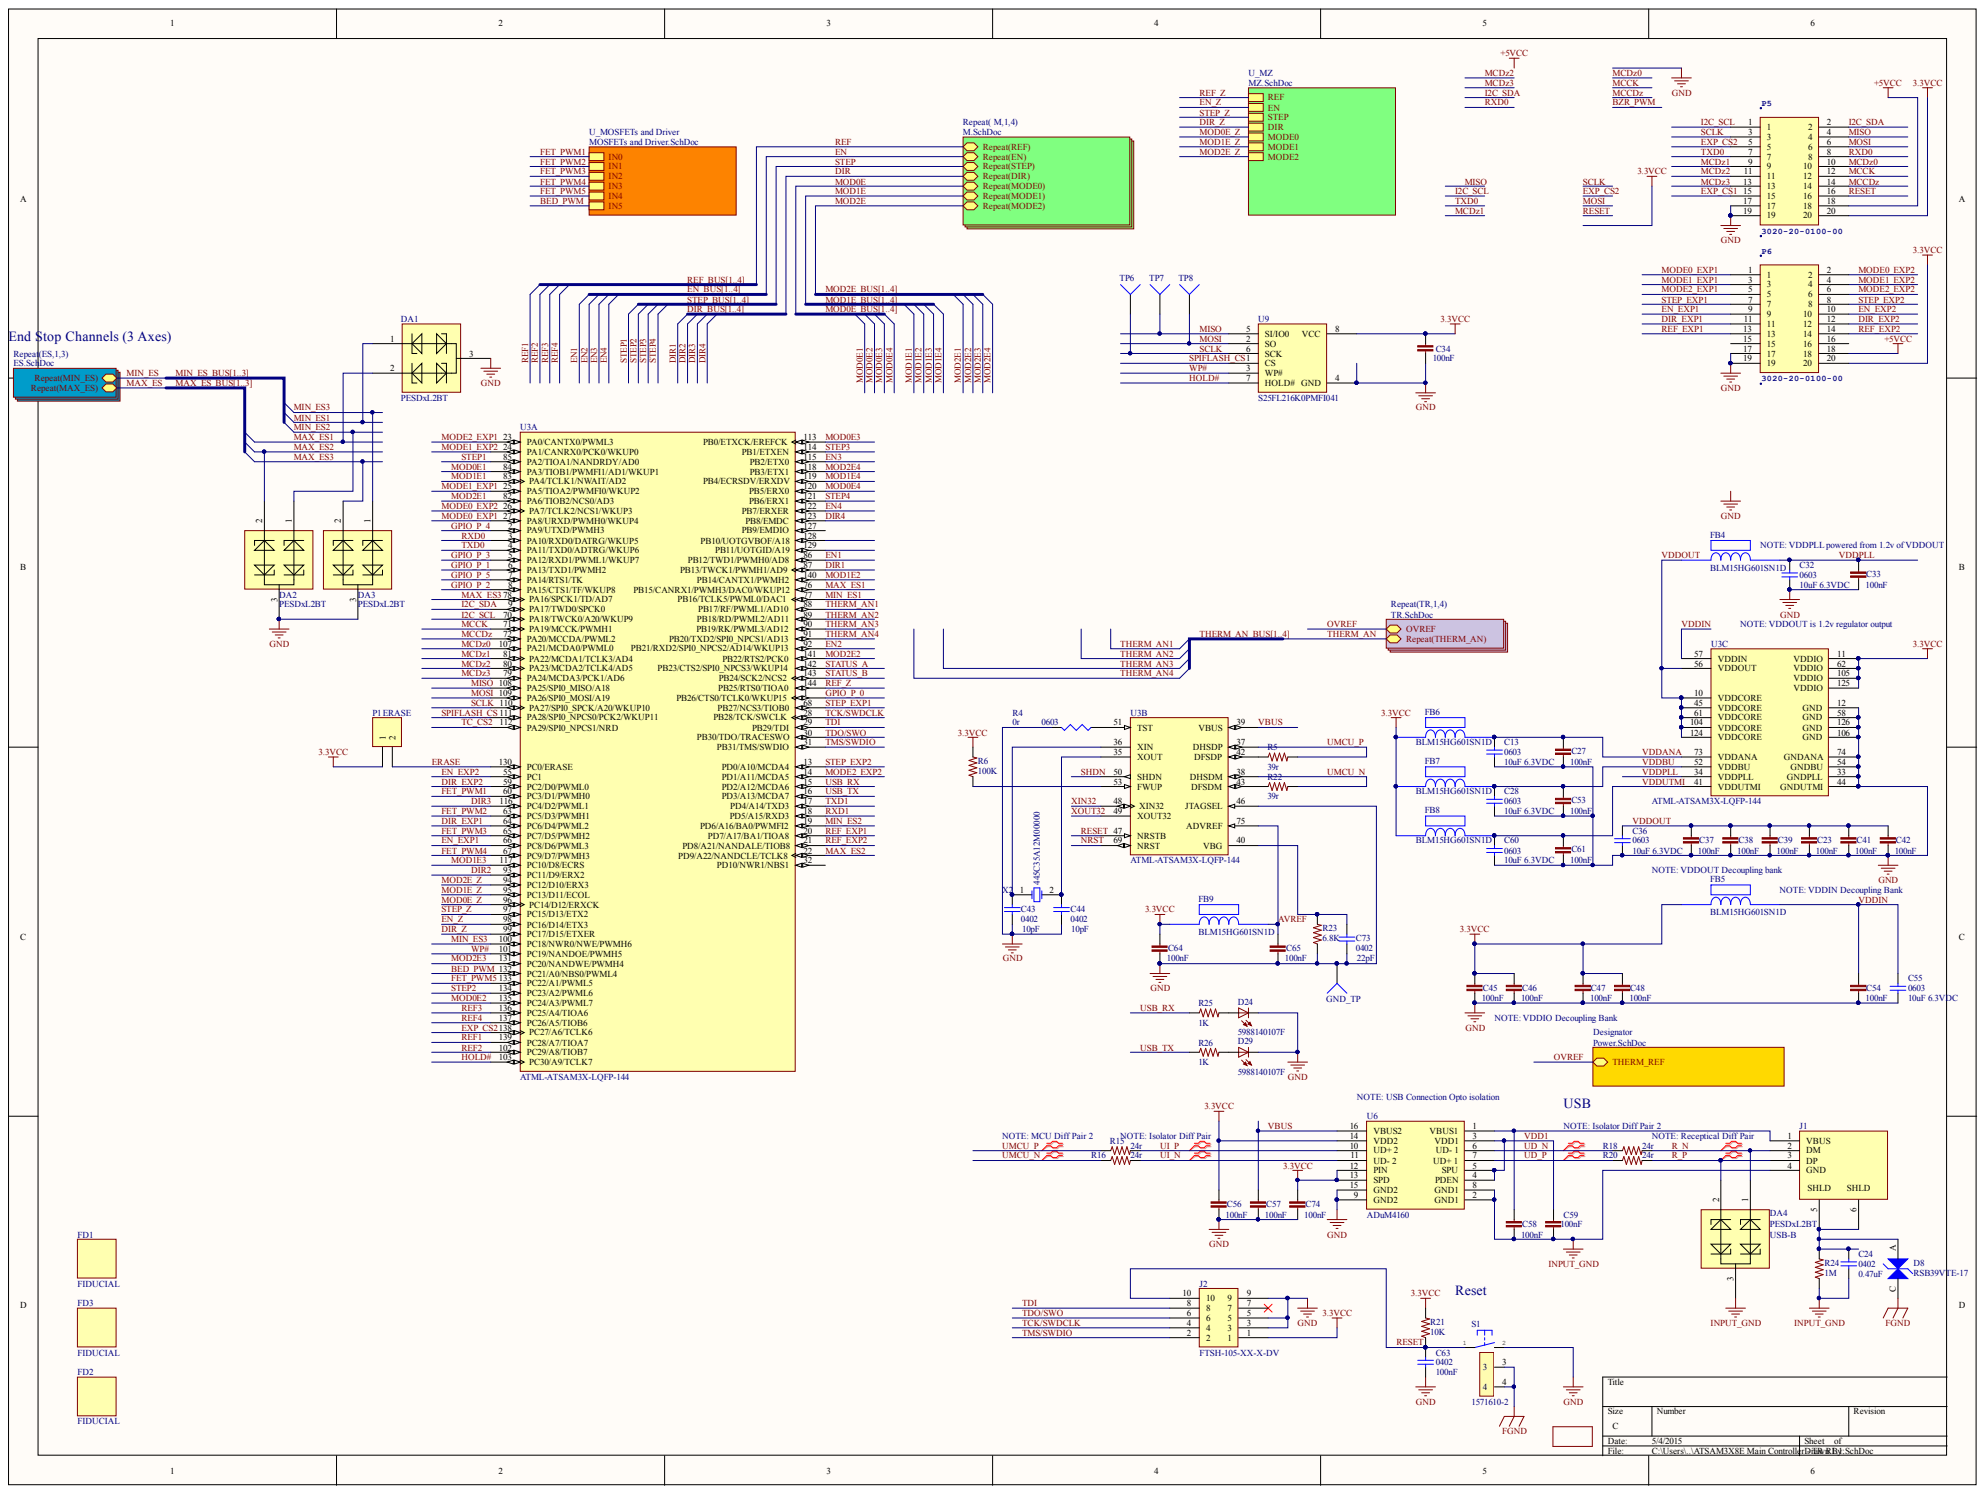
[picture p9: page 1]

End Stop Channels (3 Axes)

MAX_ES | MAX_ES_BUS[1..3]

NOTE: VDDPLL powered from 1.2v of VDDOUT

NOTE: VDDOUT is 1.2v regulator output

NOTE: VDDOUT Decoupling bank

NOTE: VDDIN Decoupling Bank

NOTE: VDDIO Decoupling Bank

NOTE: USB Connection Opto isolation

VDD2 14 | | VDD1 NOTE: Receptical Diff Pair | VBUS 1 SHLD SHLD

NOTE: Isolator Diff Pair 2

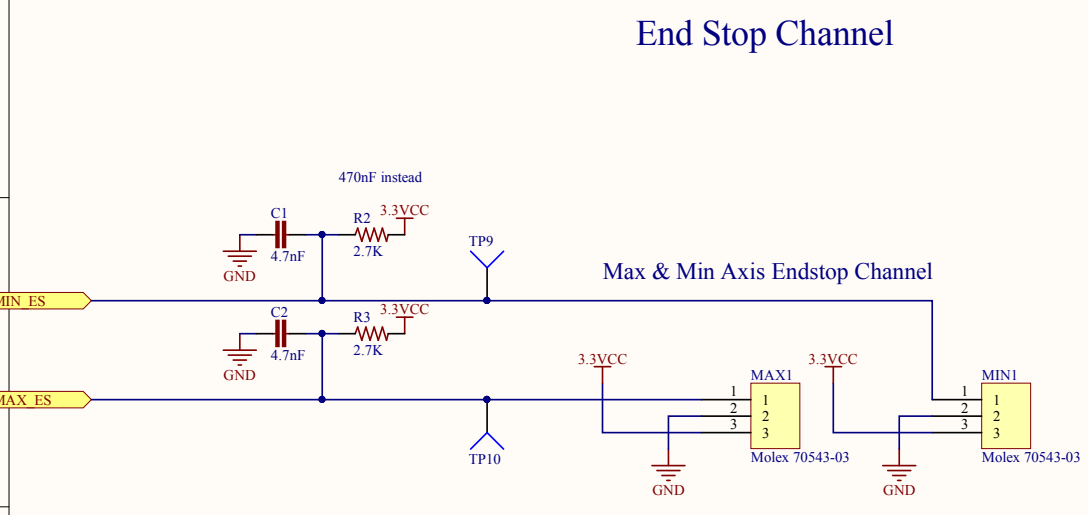
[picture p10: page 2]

Max & Min Axis Endstop Channel

C2 | 3.3VCC

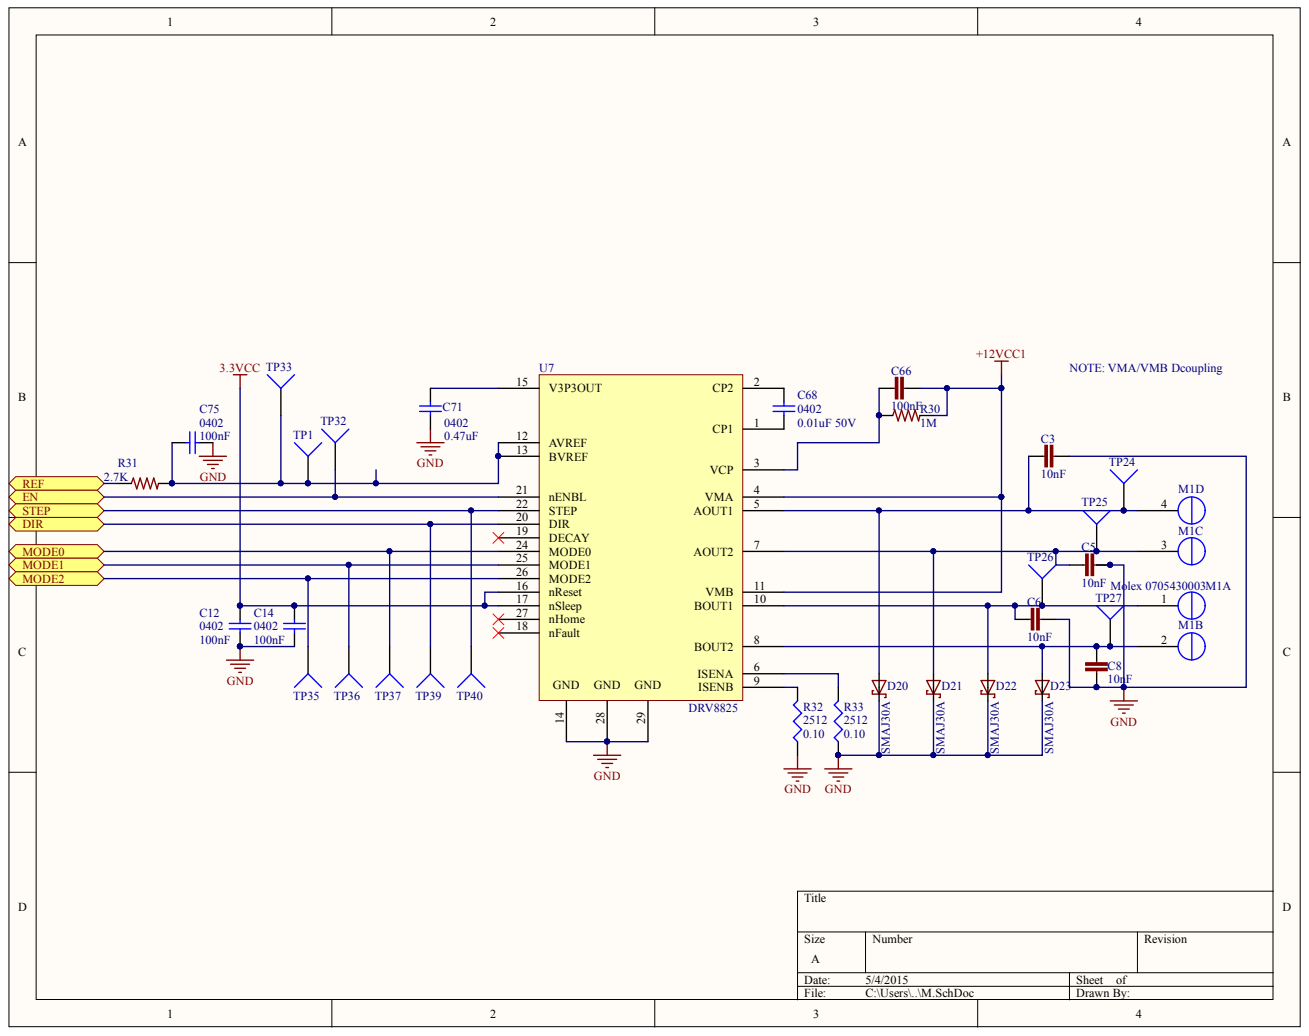
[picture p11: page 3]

17 | D20
nHome 27

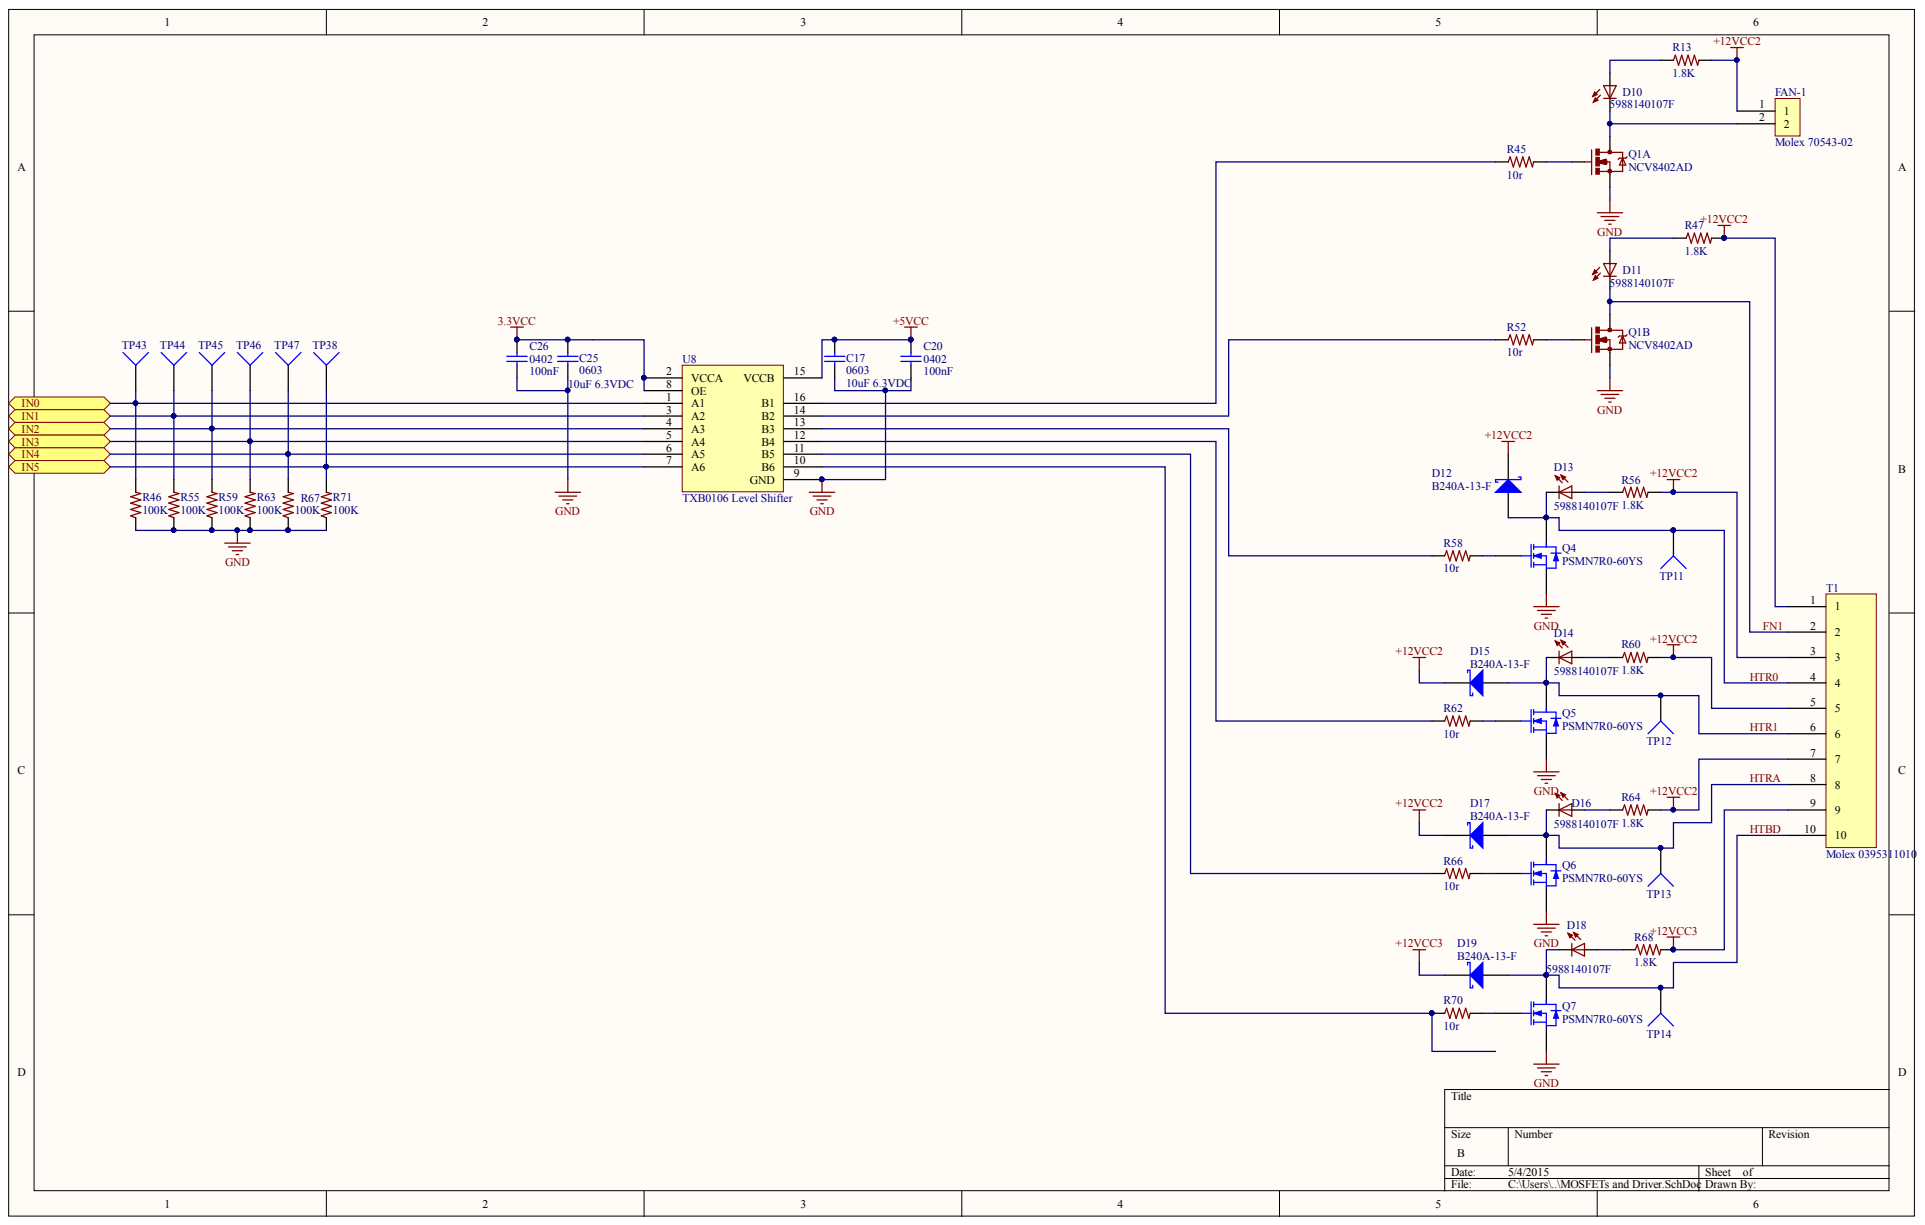
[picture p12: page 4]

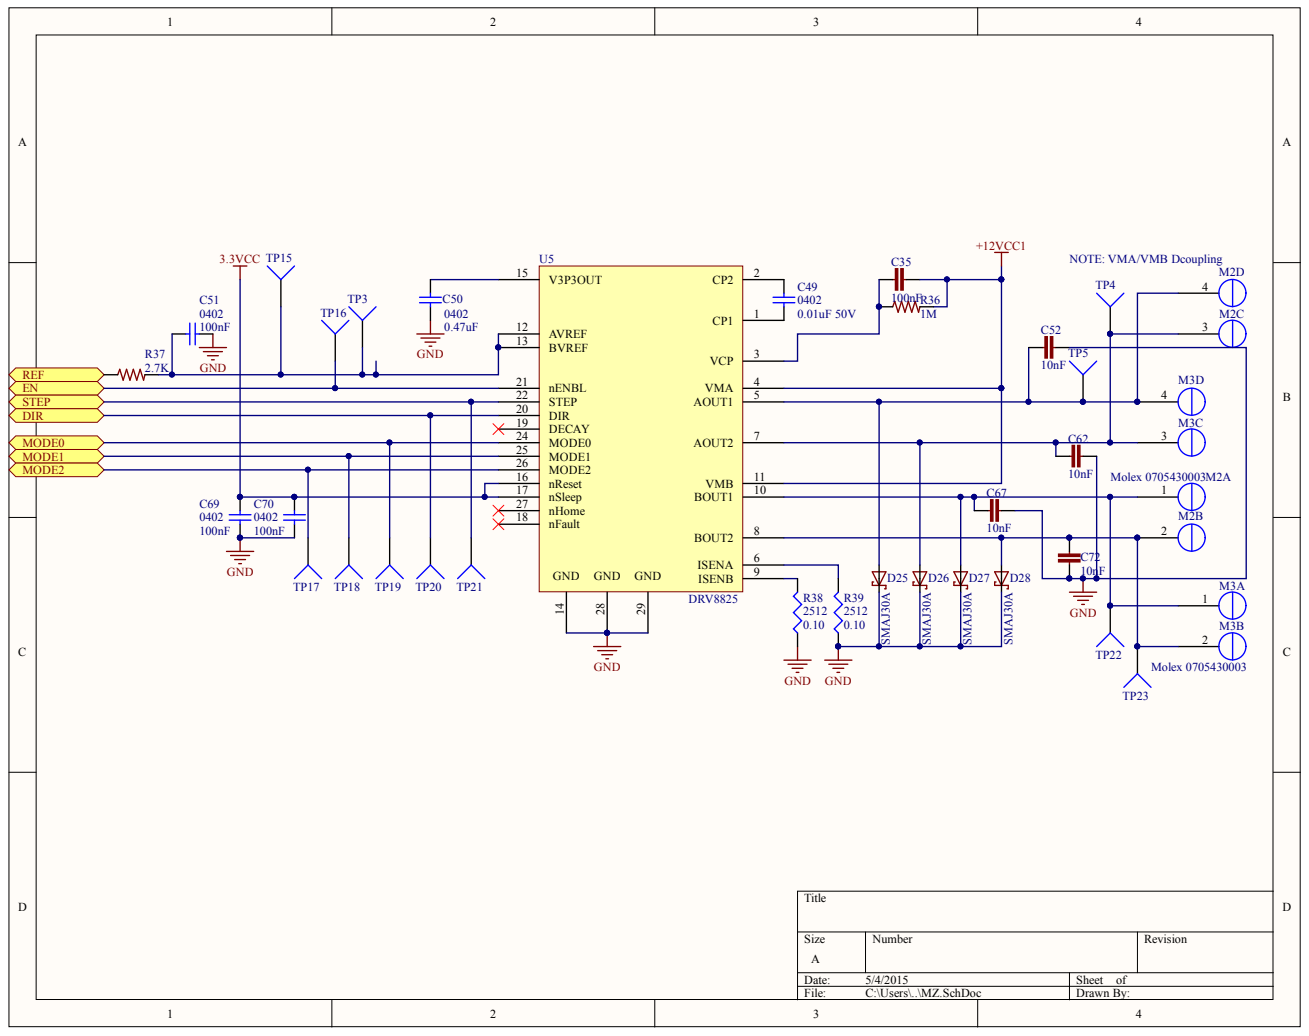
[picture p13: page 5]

17 | C67
nHome 27 | 2

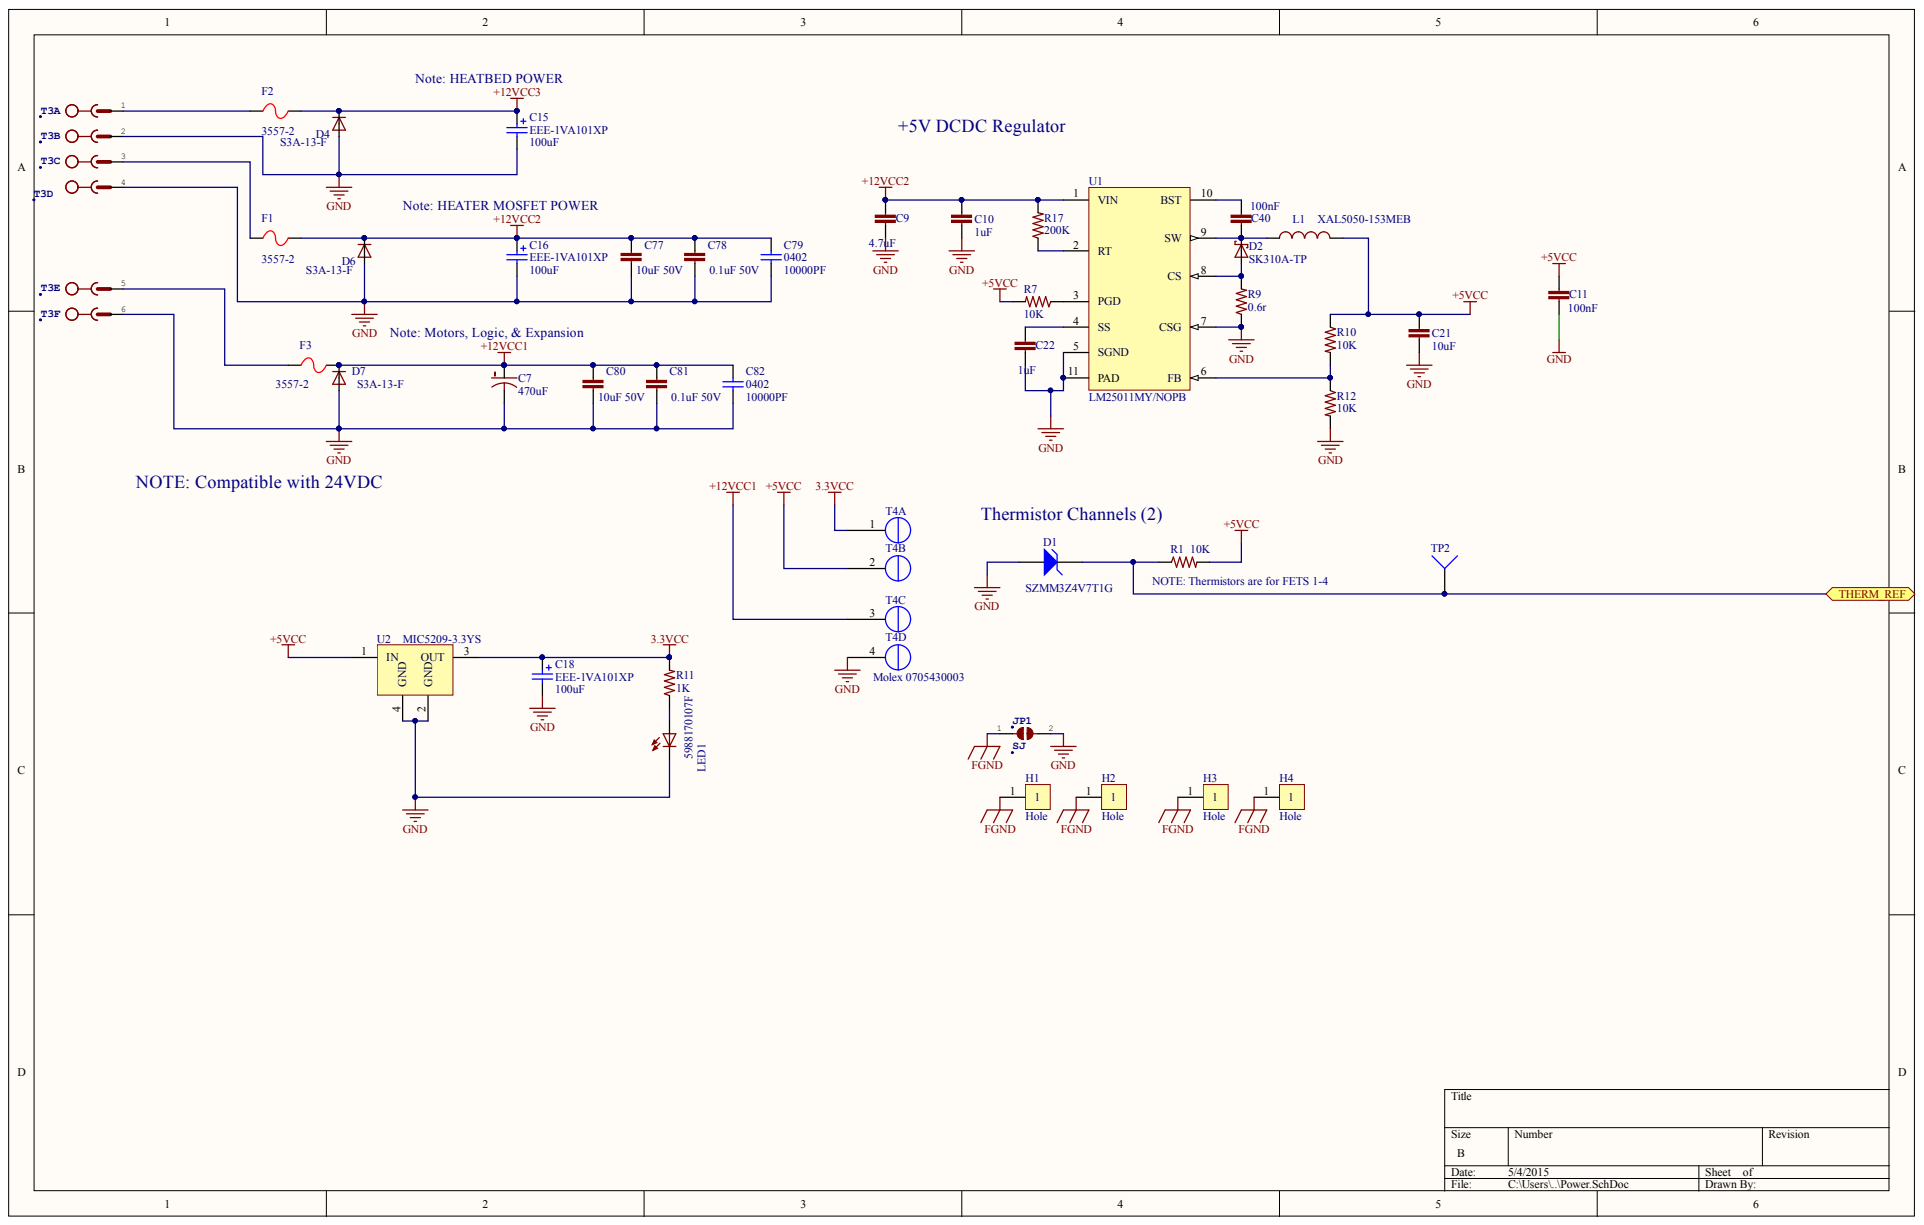
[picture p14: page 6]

Note: HEATER MOSFET POWER

Note: Motors, Logic, & Expansion

NOTE: Thermistors are for FETS 1-4

Size B | Number | Revision

Date: 5/4/2015 | Sheet of
File: C:\Users\..\Power.SchDoc | Drawn By:

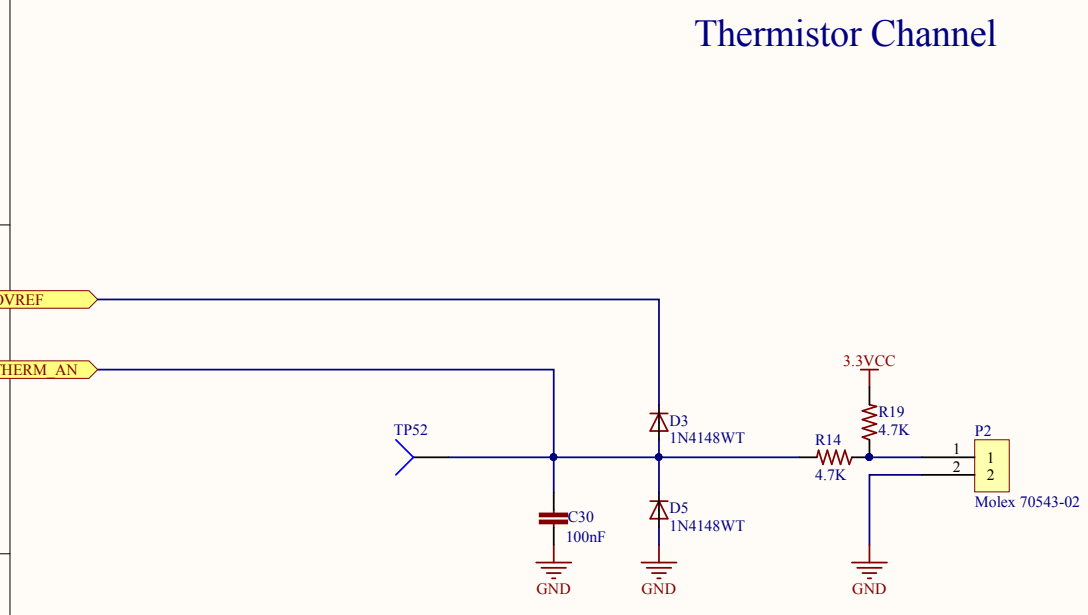
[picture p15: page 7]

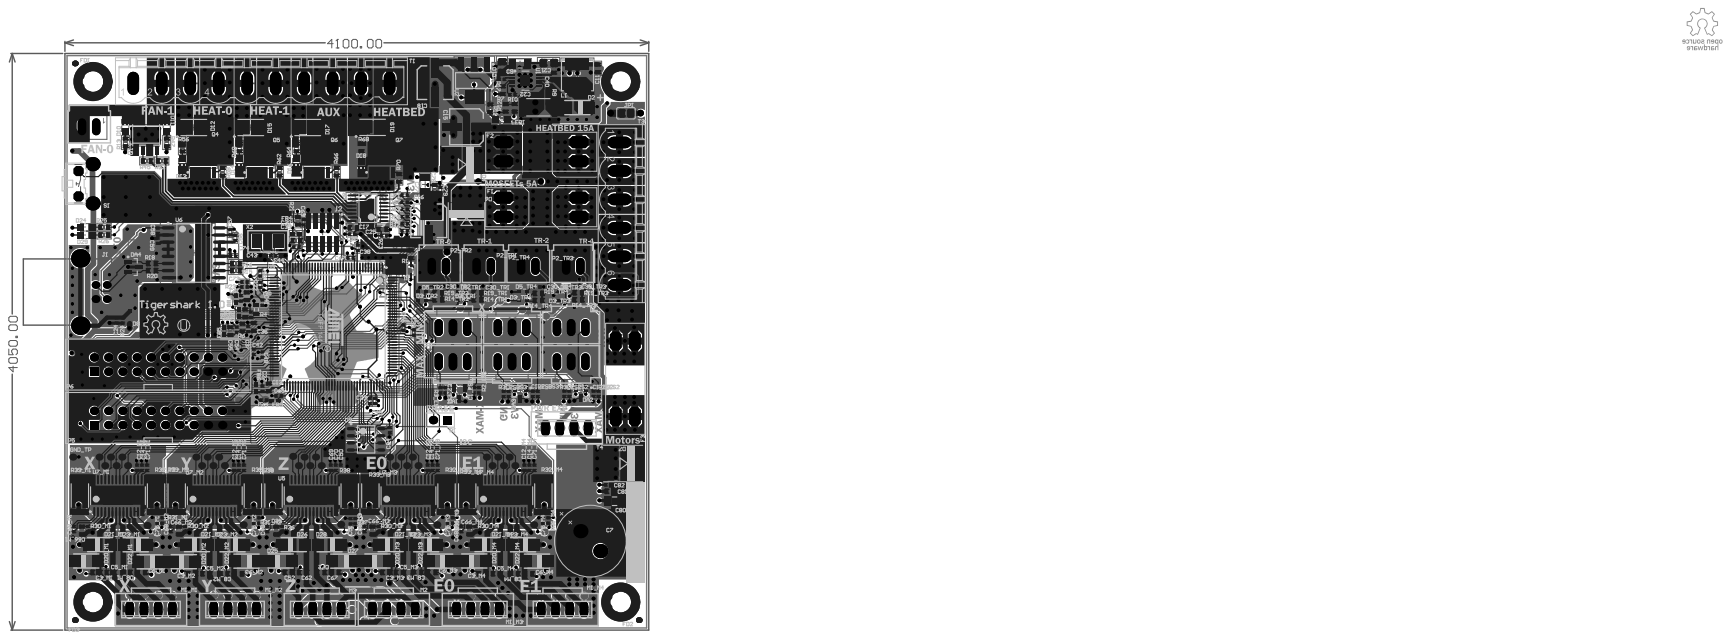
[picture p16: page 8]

Bill of Materials | <Parameter Title not found>
Source Data From: | Tigershark 3D rev2 PreProduction Thermistors Version.PrjPcb
Project: | | Tigershark 3D rev2 PreProduction Thermistors Version.PrjPcb
Variant: | | None
Creation Date: 5/4/2015 | 11:30:47 PM
Print Date: | 04-May-15 | 11:32:47 PM
Footprint | Comment | LibRef | Designator | Description | Quantity
C0402 | 4.7nF | CC0402KRX7R8 BB472 | C1_ES1 | CAP CER 0402 4.7nF 25V 10% X7R | 1
C0402 | 4.7nF | CC0402KRX7R8 BB472 | C1_ES2 | CAP CER 0402 4.7nF 25V 10% X7R | 1
C0402 | 4.7nF | CC0402KRX7R8 BB472 | C1_ES3 | CAP CER 0402 4.7nF 25V 10% X7R | 1
C0402 | 4.7nF | CC0402KRX7R8 BB472 | C2_ES1 | CAP CER 0402 4.7nF 25V 10% X7R | 1
C0402 | 4.7nF | CC0402KRX7R8 BB472 | C2_ES2 | CAP CER 0402 4.7nF 25V 10% X7R | 1
C0402 | 4.7nF | CC0402KRX7R8 BB472 | C2_ES3 | CAP CER 0402 4.7nF 25V 10% X7R | 1
C0603 | 10nF | C1608X7R1E10 3K080AA | C3_M1 | CAP CER 0603 10nF 25V 10% X7R | 1
C0603 | 10nF | C1608X7R1E10 3K080AA | C3_M2 | CAP CER 0603 10nF 25V 10% X7R | 1
C0603 | 10nF | C1608X7R1E10 3K080AA | C3_M3 | CAP CER 0603 10nF 25V 10% X7R | 1
C0603 | 10nF | C1608X7R1E10 3K080AA | C3_M4 | CAP CER 0603 10nF 25V 10% X7R | 1
C0603 | 10nF | C1608X7R1E10 3K080AA | C5_M1 | CAP CER 0603 10nF 25V 10% X7R | 1
C0603 | 10nF | C1608X7R1E10 3K080AA | C5_M2 | CAP CER 0603 10nF 25V 10% X7R | 1
C0603 | 10nF | C1608X7R1E10 3K080AA | C5_M3 | CAP CER 0603 10nF 25V 10% X7R | 1
C0603 | 10nF | C1608X7R1E10 3K080AA | C5_M4 | CAP CER 0603 10nF 25V 10% X7R | 1
C0603 | 10nF | C1608X7R1E10 3K080AA | C6_M1 | CAP CER 0603 10nF 25V 10% X7R | 1
C0603 | 10nF | C1608X7R1E10 3K080AA | C6_M2 | CAP CER 0603 10nF 25V 10% X7R | 1
C0603 | 10nF | C1608X7R1E10 3K080AA | C6_M3 | CAP CER 0603 10nF 25V 10% X7R | 1
C0603 | 10nF | C1608X7R1E10 3K080AA | C6_M4 | CAP CER 0603 10nF 25V 10% X7R | 1
C12,5-5 | 470uF | UPW1H471MHD 1TO | C7 | CAP ALU 470uF 50V 20% | 1
C0603 | 10nF | C1608X7R1E10 3K080AA | C8_M1 | CAP CER 0603 10nF 25V 10% X7R | 1
C0603 | 10nF | C1608X7R1E10 3K080AA | C8_M2 | CAP CER 0603 10nF 25V 10% X7R | 1
C0603 | 10nF | C1608X7R1E10 3K080AA | C8_M3 | CAP CER 0603 10nF 25V 10% X7R | 1
C0603 | 10nF | C1608X7R1E10 3K080AA | C8_M4 | CAP CER 0603 10nF 25V 10% X7R | 1
C1206 | 4.7uF | C1206C475K5P ACTU | C9 | CAP CER 1206 4.7uF 50V 10% X5R | 1
C0805 | 1uF | GRM21BR71H10 5KA12L | C10 | CAP CER 0805 1uF 50V 10% X7R | 1
C0603 | 100nF | C0603C104K5R ACTU | C11 | CAP CER 0603 100nF 50V 10% X7R | 1
C0402 | 0402 | 100nF C0402 - GRM155R71C10 4KA88D | C12_M1 | Capacitor (Semiconductor SIM Model) | 1
C0402 | 0402 | 100nF C0402 - GRM155R71C10 4KA88D | C12_M2 | Capacitor (Semiconductor SIM Model) | 1
C0402 | 0402 | 100nF C0402 - GRM155R71C10 4KA88D | C12_M3 | Capacitor (Semiconductor SIM Model) | 1
C0402 | 0402 | 100nF C0402 - GRM155R71C10 4KA88D | C12_M4 | Capacitor (Semiconductor SIM Model) | 1
C0603 | 0603 | C1608JB0J106 K080AB | C13 | CAP CER 10UF 6.3V 10% JB 0603 | 1
C0402 | 0402 | 100nF C0402 - GRM155R71C10 4KA88D | C14_M1 | Capacitor (Semiconductor SIM Model) | 1
C0402 | 0402 | 100nF C0402 - GRM155R71C10 4KA88D | C14_M2 | Capacitor (Semiconductor SIM Model) | 1
C0402 | 0402 | 100nF C0402 - GRM155R71C10 4KA88D | C14_M3 | Capacitor (Semiconductor SIM Model) | 1
C0402 | 0402 | 100nF C0402 - GRM155R71C10 4KA88D | C14_M4 | Capacitor (Semiconductor SIM Model) | 1

EEE-

1VA101XP | EEE-1VA101XP | EEE-1VA101XP | C15 | CAP ALUM 100UF 35V 20% SMD | 1

EEE-

1VA101XP | EEE-1VA101XP | EEE-1VA101XP | C16 | CAP ALUM 100UF 35V 20% SMD | 1
C0603 | 0603 | C1608JB0J106 K080AB | C17 | CAP CER 10UF 6.3V 10% JB 0603 | 1

EEE-
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

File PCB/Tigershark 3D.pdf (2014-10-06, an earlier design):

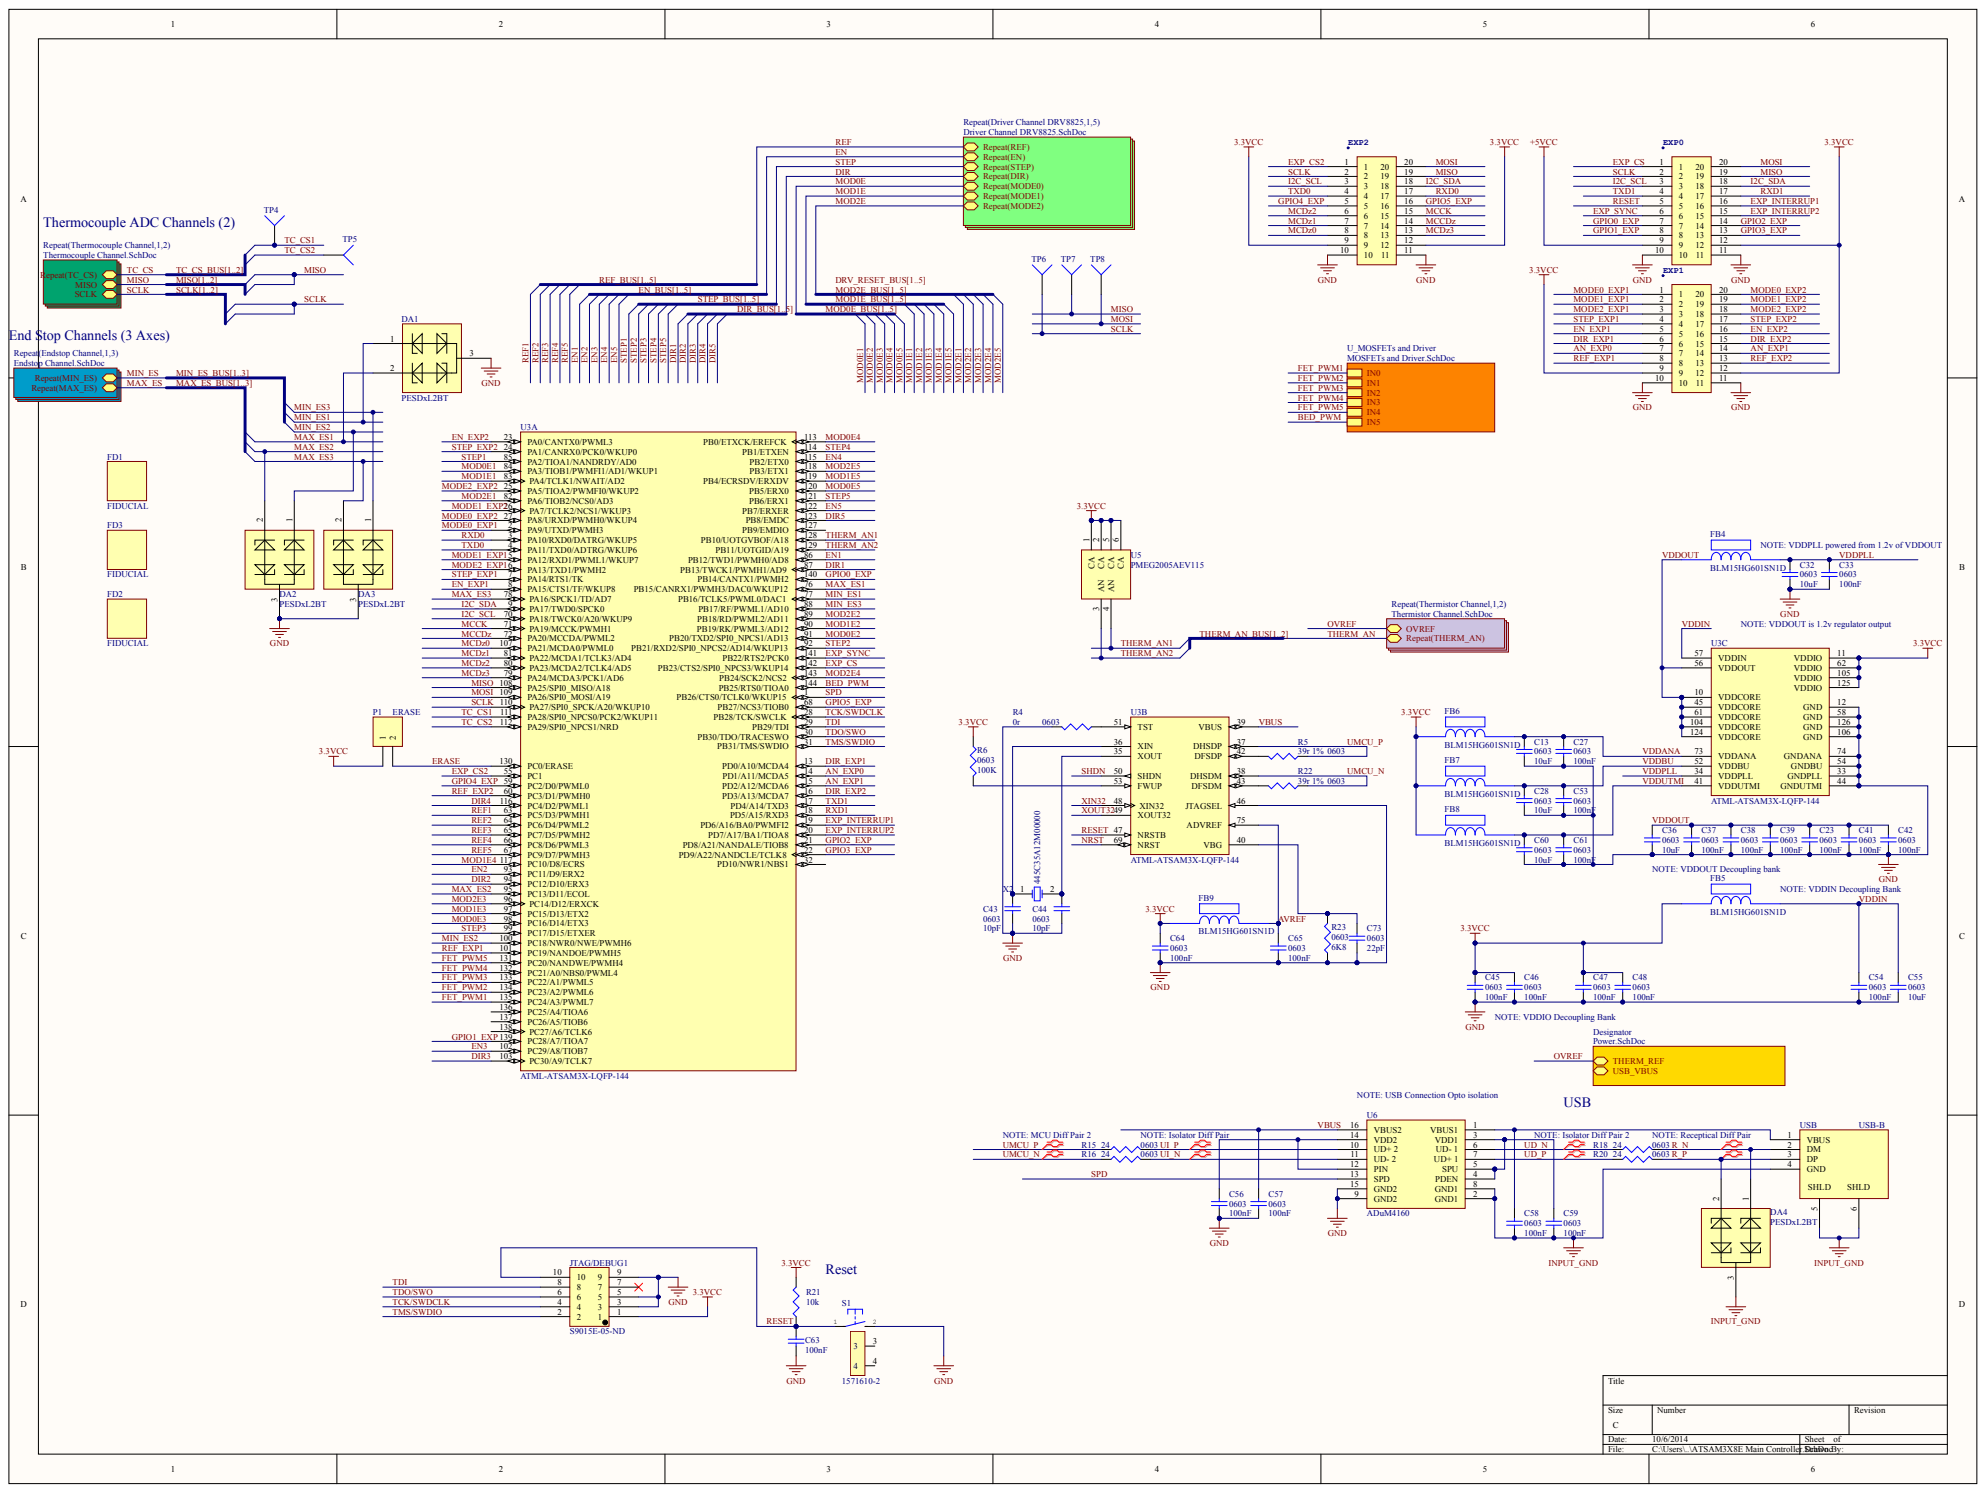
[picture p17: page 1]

End Stop Channels (3 Axes)

NOTE: VDDPLL powered from 1.2v of VDDOUT

NOTE: VDDOUT is 1.2v regulator output

NOTE: VDDOUT Decoupling bank

NOTE: VDDIN Decoupling Bank

NOTE: VDDIO Decoupling Bank

NOTE: USB Connection Opto isolation

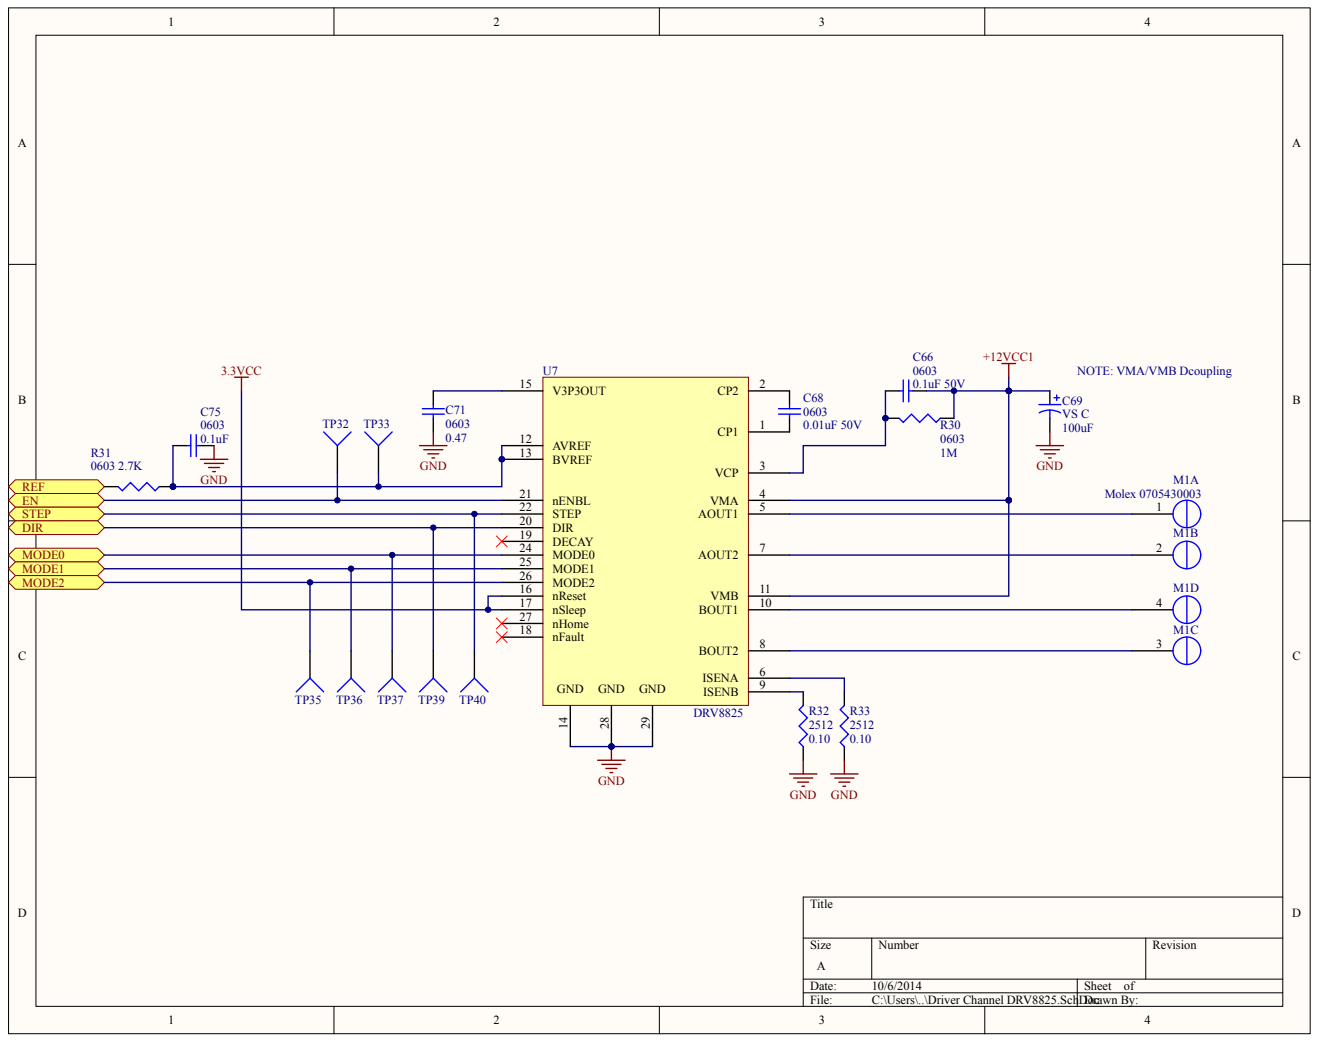
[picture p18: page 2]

C71 | AVREF 12 | C68 0603 0.01uF 50V

BVREF 13

17
nHome 27

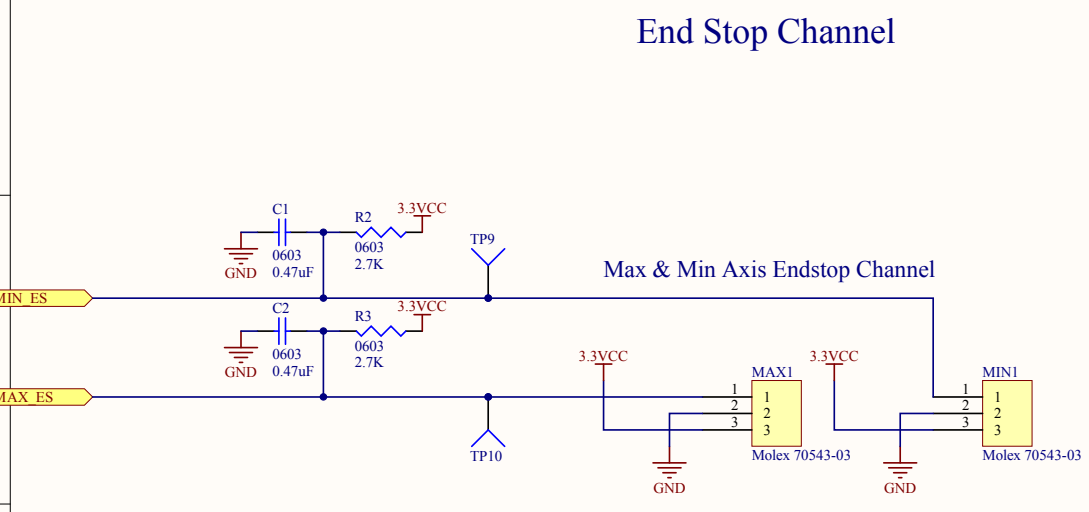
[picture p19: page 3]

Max & Min Axis Endstop Channel

C2 | 3.3VCC

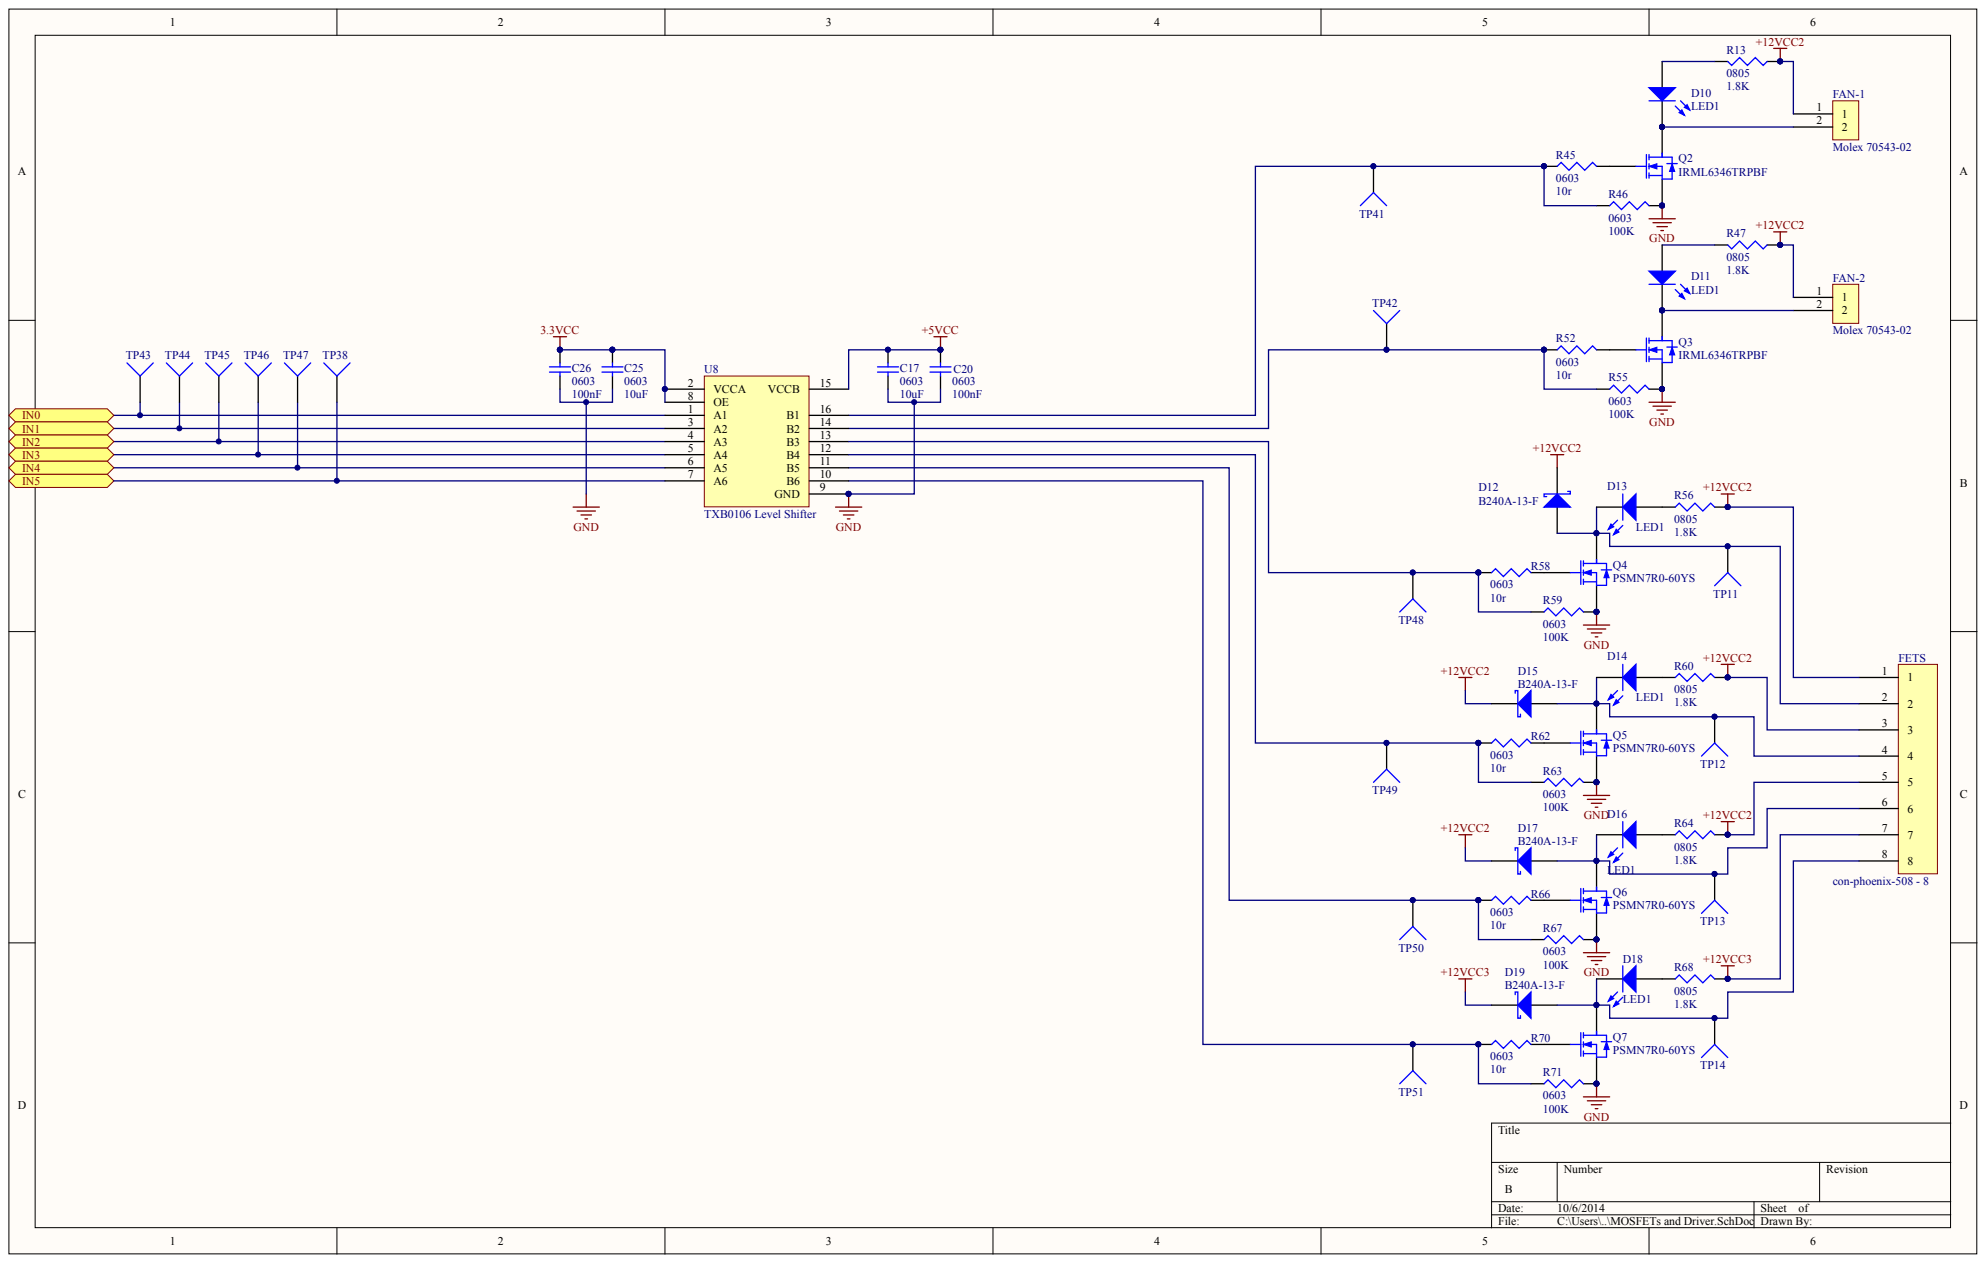
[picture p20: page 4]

Size | Number | Revision B

Date: 10/6/2014 | Sheet of
File: C:\Users\..\MOSFETs and Driver.SchDoc | Drawn By:


Note: Motors, Logic, & Expansion
+12VCC1

NOTE: Thermistors are for FETS 1-4

GND

Logic Power Supply Select Jumper
LittleFuse F1210

Size B | Number | Revision

Date: 10/6/2014 | Sheet of
File: C:\Users\..\Power.SchDoc | Drawn By:




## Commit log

2014-08-06 Initial Commit
    Forked from ZMBo, a Arduino compatible (DUE) 3D pritner board designed
    to run TinyG as well as popular ARM firmwares.
    [ATSAM3X8E Main Controller.SchDoc, ATSAM4E16EA_AU Main Controller.SchDoc, Arduino DUE Interface.SchDoc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]
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2014-08-27 Big CHanges
    Following the discussion with Alden Hart and Johnny Russel the following
    changes have been added and are ongoing:
    - power connection for motor voltage closer to actual motor current
    paths
    - endstops moved next to temp circuitry
    - smart port moved to edge of board (power side)
    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
    [ATSAM3X8E Main Controller.SchDoc, MOSFETs and Driver.SchDoc, Power.SchDoc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]
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2014-09-07 Expansion Port
    Smart expansion port mostly routed. Overall board route looking quite
    good. Next commit should be the last.
    [ATSAM3X8E Main Controller.SchDoc, MOSFETs and Driver.SchDoc, Tigershark 3D R1.4.PcbDoc]
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2014-09-12 Updates
    Power section rerouted to accommodate 15A load for heatbed and to make
    sure the crowbar circuit for each power port will blow before the PCB
    does in the event of a short.
    [ATSAM3X8E Main Controller.SchDoc, MOSFETs and Driver.SchDoc, Power.SchDoc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]
2014-09-14 Last Minute Fixes
    Manually inspected every section of the PCB in close detail, focusing on
    each layer (Altium Shift+s). Small bugs and mistakes were fixed. Bottom
    traces cleaned up.
    [ATSAM3X8E Main Controller.SchDoc, Tigershark 3D R1.5.PcbDoc, Tigershark 3D.PrjPcb]
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2014-09-19 Wave Soldering Fix
    GPIO expansion connector flipped to prevent bridging during wave
    soldering process. 4D systems display connector changed to standard
    header for prototype.
    [ATSAM3X8E Main Controller.SchDoc, Tigershark 3D R1.5.PcbDoc]
2014-09-22 Fiducials and Test points
    Fiducials added to 3 out of four corners for pick and place assembly.
    Test points added to stepper signals, SPI signals, and power. Also 0 ohm
    resistors have been added to the PSU for safely bringing the board
    online the first time.
    [ATSAM3X8E Main Controller.SchDoc, Driver Channel DRV8825.SchDoc, MOSFETs and Driver.SchDoc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]
2014-09-22 Final Changes
    Display port fro 4D systems display removed. All external peripherals
    should be connected through the smart port and if level shifting is
    required it must be included on the peripheral or if the peripheral is
    off the shelf an adapter board needs to carry any level shifting or
    additional circuitry.
    [ATSAM3X8E Main Controller.SchDoc, Power.SchDoc, Tigershark 3D R1.5.PcbDoc]
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2014-09-23 Fab Rev
    Finalized for fab, pending short discussion with team before sent out.
    [Power.SchDoc, Tigershark 3D R1.5.PcbDoc, Tigershark 3D.PrjPcb]
2014-09-24 MOSFET Topology change
    The gate driver has now become unavailable to source. It has been
    replaced with a level translator that will make the 3,3v PWM from the
    ATSAM into 100mA 5V capable of driving MOSFET circuit.
    [ATSAM3X8E Main Controller.SchDoc, MOSFETs and Driver.SchDoc, Power.SchDoc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]
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2014-09-24 Finalized Changes
    Changes to a levelshifter MOSFET driving topology complete. PDF inline
    with schematic and board. Board previews inline with latest design.
    [ATSAM3X8E Main Controller.SchDoc, MOSFETs and Driver.SchDoc, Tigershark 3D R1.6.PcbDoc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]
2014-09-25 power topology change
    insane last minute fixes. power topology transitioned over to 2A 5v dcdc
    into a 500mA 3.3v LDO. driver resets also tied high, lots of pins free.
    also LEDs gone.
    [ATSAM3X8E Main Controller.SchDoc, Driver Channel DRV8825.SchDoc, MOSFETs and Driver.SchDoc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]
2014-09-26 Last MInute OVerhaul almost done
    Last minute overhaul almost finished. Just need to review it more.
    [ATSAM3X8E Main Controller.SchDoc, MOSFETs and Driver.SchDoc, Power.SchDoc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]
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2014-09-30 Cap and Breakout
    Power cap values changed and remaining IO broken out to additional EXP
    connector.
    [ATSAM3X8E Main Controller.SchDoc, MOSFETs and Driver.SchDoc, Power.SchDoc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]
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2014-10-04 USB and Expansion Refactor
    USB icoupler isolator circuit under rework. Expansion ports rethought
    out and new pins are being mapped.
    [ATSAM3X8E Main Controller.SchDoc, Tigershark 3D R1.8.PcbDoc, Tigershark 3D.PrjPcb]
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2014-10-05 Smart Port
    New Smart port traced in. Next is GPIO port and rest of MOSFET power
    makeover.
    [ATSAM3X8E Main Controller.SchDoc, Tigershark 3D R1.8.PcbDoc]
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2014-10-07 DRC Errors Resolved
    DRC errors resolved.
    [Tigershark 3D R1.8.PcbDoc]
2014-10-07 Layer Stackup
    Layer stackup optimized for ADI iCoupler device on the USB section.
    [Tigershark 3D R1.8.PcbDoc, Tigershark 3D.PrjPcb]
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2014-10-08 Layer Stackup Again
    Let's see if we got it right this time XD
    [Tigershark 3D R1.8.PcbDoc, Tigershark 3D.PrjPcb]
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2014-10-09 Done
    Finished revising and retracing around new DRC specifications. Should be
    off to the fab now.
    [Tigershark 3D R1.8.PcbDoc, Tigershark 3D.PrjPcb, Tigershark-Panel.PcbDoc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]
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2015-01-01 Rev2
    Driver topology revised to include EMI compliance filtering and back EMF
    protection. Board topology currently being revised for smaller size.
    About 10 square inches shaved off thus far.
    [ATSAM3X8E Main Controller.SchDoc, M.SchDoc, MOSFETs and Driver.SchDoc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]
2015-01-02 PCB resized
    PCB resized to 4X4.7 inches square/rectangular. Pending changover to new
    smaller cheaper expansion connectors. Next rerouting the connections
    between subsystems.
    [ES.SchDoc, Power.SchDoc, Tigershark 3D R1.8.PcbDoc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]
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2015-01-05 Bottom OVerlay and tidying
    layout tidied up a bit. Bottom overlay texts modified.
    [Tigershark 3D R2.PcbDoc]
2015-01-06 Expansion
    RAMBo formfactor achieved. fixes from discussion with Johnny added.
    Expansion connectorsand SD card slot added. Routing second expansion
    connector then done.
    [ATSAM3X8E Main Controller.SchDoc, Power.SchDoc, Tigershark 3D R1.8.PcbDoc]
2015-01-09 Additional expanson
    additional expansion IO added. 6 GPIO pins and 3v3/GND on 2.54mm
    standard pin headers.
    [ATSAM3X8E Main Controller.SchDoc, MOSFETs and Driver.SchDoc, MZ.SchDoc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]
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2015-01-27 Expansion
    Expansion headers changed, to shrouded 2.54mm through hole connectors
    with key. These are more hacker friendly and cost effective.
    [ATSAM3X8E Main Controller.SchDoc, MOSFETs and Driver.SchDoc, Tigershark 3D R2.2.PcbDoc]
2015-01-28 Expansion Finished
    New expansion headers added and signals routed. All PWM errors cleared.
    Now cleaning up libraries and beginning the 4 thermistor version.
    [ATSAM3X8E Main Controller.SchDoc, Tigershark 3D R2.2.PcbDoc, Tigershark 3D rev2 PreProduction Thermistors Version.PrjPcb]
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2015-03-17 Updates
    Thermistor Version is now the most up to date version and it is now the
    priority. USB isolator circuit has been fixed and brought in line with
    the reference schematic, based on our findings with Prototype 1. Thermal
    relief design rules have been implemented for power/ground plane connect
    as well as polygon pours, all throughhole parts should achieve 80% PTH.
    [ATSAM3X8E Main Controller - RRDC.SchDoc, ATSAM3X8E Main Controller - TR - RRDC.SchDoc, ATSAM3X8E Main Controller - TR.SchDoc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]
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2015-03-26 Production overhaul
    High noise filters added to heater and motor power (logic runs off the
    heater power input), board is generally cleaned up, thermistor section
    revised, power section revised, thermal relief revised (almost done).,
    and added expansion power.
    [ATSAM3X8E Main Controller - TR R1.1.SchDoc, ES.SchDoc, Power.SchDoc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]
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2015-04-01 Johnny's List
    Johnny's list implemented into the board. New fuses and diode on heat
    input, test points for vref adjusted, and fet PWM testpoints adjusted.
    [ATSAM3X8E Main Controller - TR R1.1.SchDoc, M.SchDoc, MZ.SchDoc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]
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2015-04-09 Engineering Changes/Workstation Sync
    Moving to mobile workstation, also applying engineering changes as per
    requested by Johnnyr and Tonokip
    [ATSAM3X8E Main Controller - TR R1.1.SchDoc, ES.SchDoc, MOSFETs and Driver.SchDoc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]
2015-04-10 Major Update
    Power supply revised to reduse noise feedback from inductor through
    fuses, fan circuit switched to the new design on mini-rambo, fuse diodes
    switched to higher voltage part for more fuse options. RAMBo 6 position
    power input connector in the same spot as the RAMBo. RAMBo formfactor
    overall better realized.
    [ATSAM3X8E Main Controller - TR R1.1.SchDoc, MOSFETs and Driver.SchDoc, Power.SchDoc]
2015-04-12 cleanup
    Cleaning up traces, via stitching, shortening paths to ground.
    [ATSAM3X8E Main Controller - TR R1.1.SchDoc]
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2015-04-20 Mid Update
    Mid update. Pushing again so Johnny can see the file. Note that this
    push is incomplete and a work in process of change integration.
    [CSV Bill of Materials-Mini-Rambo.csv, M.SchDoc, MZ.SchDoc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]
2015-04-21 Project Cleanup
    Project cleaned up, errors resolved, designator conflicts resolved.
    [ATSAM3X8E Main Controller - TR R1.1.SchDoc, Power.SchDoc, Tigershark 3D rev2 PreProduction Thermistors Version.PrjPcb]
2015-05-05 Overhaul
    Ground shielding for logic level voltage rails, thermal relief added for
    wave soldering of high voltage power section throughole components.
    Overall cleanup of board.
    [ATSAM3X8E Main Controller - TR R1.1.SchDoc, M.SchDoc, MZ.SchDoc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]
2015-05-07 Halfway through list
    dcdc 5v feedbackloop on bottom layer cleanup
    DONE
    motor output test points, prevent bridging
    DONE
    vref test point direct connect less via DONE
    remove traces beneath icoupler , nothing under it!!!!!!!!!!!!!!!!! DONE
    label power expansion pins DONE
    erase button/jumper, ask rob
    DONE
    testpoint on flash chip select Done
    [ATSAM3X8E Main Controller - TR R1.1.SchDoc, M.SchDoc, MZ.SchDoc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]
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2015-05-13 PSU Move
    powersupply moved (LDO and switching reg) to be 50 mil from board edge.
    Libraries in the process of being fixed with DRC compliant vias and
    forced tenting of the vias on thermal PAD ICs.
    [ATSAM3X8E Main Controller - TR R1.1.SchDoc]
2015-05-19 Offline DRC
    Offline DRC run several times most errors fixed still going at it.
    [ATSAM3X8E Main Controller - TR R1.1.SchDoc, M.SchDoc, MOSFETs and Driver.SchDoc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]
2015-05-20 Soldermask relief
    soldermask relief for thermal pad devices added to the relevant
    footprints (FETs and DRVs). Offline DRC violations fixed.
    [M.SchDoc, MZ.SchDoc, Tigershark 3D rev2 PreProduction Thermistors Version.PrjPcb]
2015-05-26 Thermal Relief
    The rest of the list and thermal relief fixed have been applied. Working
    on the BOM now.
    [ATSAM3X8E Main Controller - TR R1.1.SchDoc, Tigershark 3D rev2 PreProduction Thermistors Version.PrjPcb]
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2015-06-03 Hole Spacing Fix
    Hole Spacing fix to match RAMBo's exactly and Gerbers generated.
    [Tigershark-rev2-Panel.GBL, Tigershark-rev2-Panel.GBO, Tigershark-rev2-Panel.GBP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]
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2015-06-12 Test Points and Labels
    Additional tespoints added as well as labels for all test points.
    Testpoints added to both sides of each fuse, 3v3 rail, 5v rail, and fan
    outputs.
    [ATSAM3X8E Main Controller - TR R1.1.SchDoc, M.SchDoc, MOSFETs and Driver.SchDoc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]
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2015-06-15 Test Points and Labels
    Test points added to each of the JTAG signals, as well as labels for
    each test point.
    Test points added for the erase signal and a lable
    Test point added for reset as well as a label.
    Test points for usb were implemented the same way as the mini-Rambo. DRC
    check run and passed.
    [ATSAM3X8E Main Controller - TR R1.1.SchDoc]
